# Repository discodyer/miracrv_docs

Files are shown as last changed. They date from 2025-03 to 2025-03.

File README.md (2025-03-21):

# MiracRV_docs

琪迹小车相关文档教程集合

## 硬件组成部分

这部分描述了如何从零开始制作小车底盘

### 生产文件（3D打印/激光切割）

生产文件在manufacture文件夹中，包含：

- 小车底板图纸
- 无刷电机X减速器连接固定片
- 降压模块安装座
- 镭神N10P激光雷达固定座

部分零件需要额外说明，请查看[README](manufacture/README.md)

### 外购零件

外购零件清单（TODO）

### 组装

TODO

## Q&A

>Q1:从设想画图到拿到板子实现测试软件功能，小车的制作整体时间

>小车是从2025年2月7号春节后开始着手制作的，大概是到2月18号硬件部分都组装制作完成

>Q2：哪些部分是自己设计的，以及为什么要自己设计而不是使用已有的配件

>小车的上下层铝板还有无刷电机和减速器的连接板，是我自己设计并找淘宝店铺切割制作的，自己设计的原因是网上的小车底板价格较贵，并且孔位不能满足DIY的需要，我自己设计的小车，兼容了几种常见的激光雷达孔位，同时兼容meles和licheepi 4a还有MATX主板的孔位等。  
设计小车底板的图纸花费的时间并不算多，只花两天就全部设计完成了。
无刷电机和减速器的连接板是小车动力装置的一个重要零件，因为淘宝上没有卖合适的无刷电机+减速器的组合套装，正好看到淘宝上有卖一款给直流电机使用的减速器，但是电机轴兼容3.5mm的，所以我买了相同大小出轴的无刷电机，并且设计了一个连接板将无刷电机和减速器拼接起来，组装了无刷电机减速器。  
这样做的主要原因是成本低廉，并且由于采用了航模无刷电机驱动，转速相对较为稳定。并且可以直接复用无人机的飞控和电调。

>Q3：小车的软硬件详细参数（包括电机、开发板、轮胎、传感器、搭载了什么软件等）

>电机使用了N2830 1300KV电机，使用AM32四合一电调，减速器使用的是27：1的减速器。  
开发板使用的是RISC-V开发板 MilkV meles，运行了RevyOS。
轮胎使用的是麦克纳姆轮，使用的飞控是微空MicoAir743 V2飞控，使用的是自己编译的ArduRover小车固件。

> Q4：列举出小车目前已经实现的功能

>目前可以实现基本运动控制，meles开发板可以在RevyOS上运行ROS2 humble的软件包。雷达没有提供驱动，所以暂时没有使用Cartographer建图，后续会换一个激光雷达继续。

>Q5: 这个DIY过程对你有什么收获和帮助，开发中有哪些因为DIY而产生的困难，以及有哪些因为DIY而带来的特别的好处

>DIY的过程中，因为公司不能使用盗版软件，所以学习了Fusion360，但是这个设计软件在草图比较复杂的时候非常卡顿，并且有一些BUG，不过还是勉强画完了。后续切割完成后，发现了几处可以修改的地方，下一个版本可以吸取经验。激光雷达一开始是在我的电脑上的虚拟机里测试的，但是我后来才发现，厂商提供的SDK是静态编译的库，所以没办法在RISC-V架构上编译。硬件测试过程也遇到过一些问题，最开始使用的电调质量有问题，烧毁了一个电机和我的一块飞控板。

>Q6：小车未来的完善计划

>未来会在小车上充分测试ROS2在RISC-V架构上的功能，并且使用激光雷达在ROS2上实现建图导航等功能

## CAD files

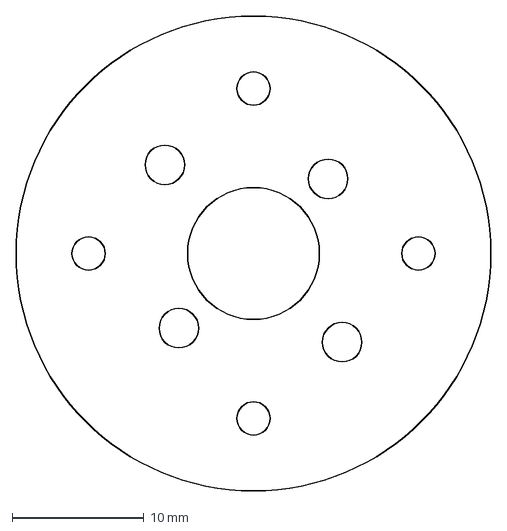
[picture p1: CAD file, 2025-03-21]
manufacture/电机固定片.dxf
36.0 x 36.0 mm

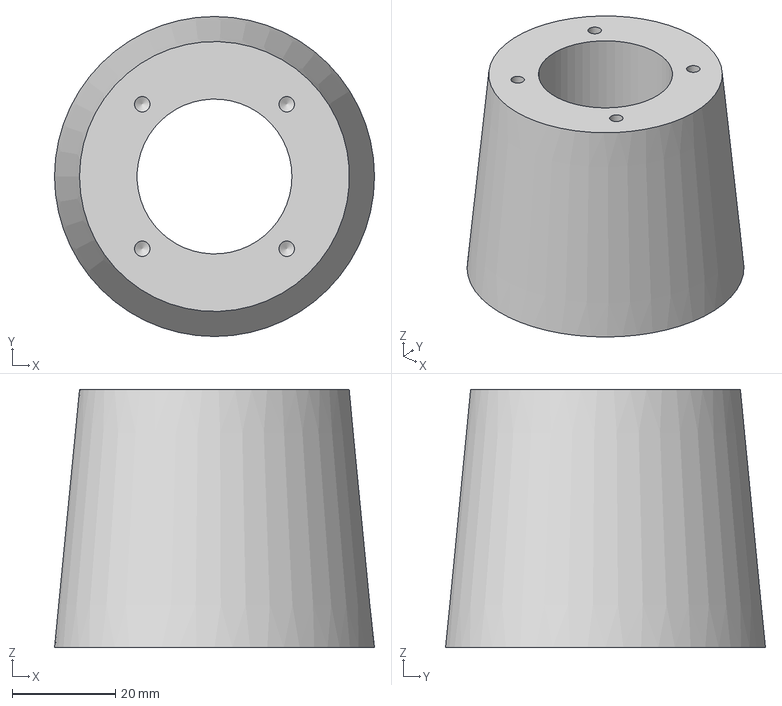
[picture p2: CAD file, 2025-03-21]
manufacture/镭神N10P激光雷达固定座.step
62.0 x 62.0 x 50.0 mm

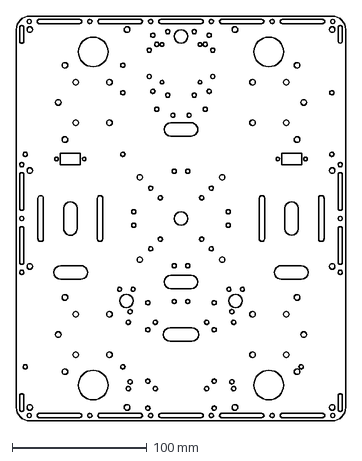
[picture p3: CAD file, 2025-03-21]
manufacture/麦轮小车底盘上板.dxf
244.0 x 300.0 mm

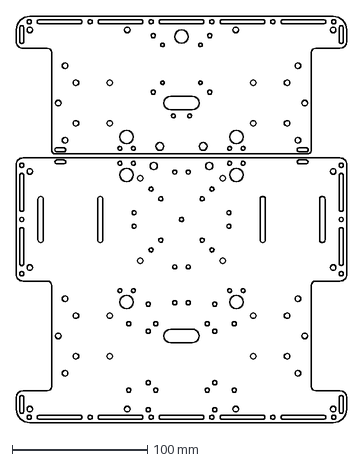
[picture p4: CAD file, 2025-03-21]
manufacture/麦轮小车底盘下板(两个件).dxf
244.0 x 300.0 mm

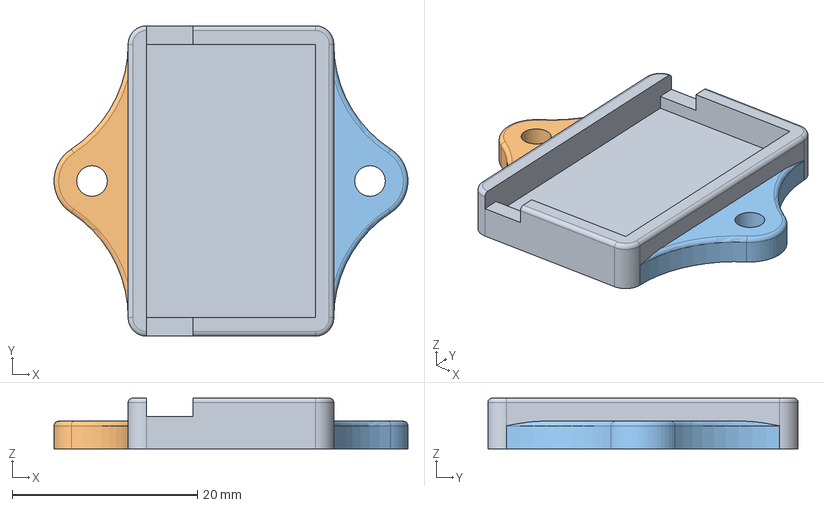
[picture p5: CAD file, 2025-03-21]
manufacture/降压模块安装座.step
38.2 x 33.5 x 5.50 mm

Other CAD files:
manufacture/电机固定片-可编辑.f3d
manufacture/镭神N10P激光雷达固定座-可编辑.f3d
manufacture/镭神N10P激光雷达固定座.stl
manufacture/降压模块安装座-可编辑.f3d
manufacture/降压模块安装座.stl
manufacture/麦轮小车底盘上板-可编辑.f3d
manufacture/麦轮小车底盘下板-可编辑.f3d

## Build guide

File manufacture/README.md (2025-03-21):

# 生产文件说明

## 小车底板图纸

兼容了几种常见的激光雷达孔位，同时兼容`meles`、`licheepi 4a`还有MATX主板的孔位

图纸包含上下两部分，其中下层板有前后两部分组成，可编辑文件可以用Fusion360打开（会很卡）

- [麦轮小车底盘上板-可编辑](麦轮小车底盘上板-可编辑.f3d) 
- [麦轮小车底盘上板-生产文件](麦轮小车底盘上板.dxf) 
- [麦轮小车底盘下板-可编辑](麦轮小车底盘下板-可编辑.f3d) 
- [麦轮小车底盘下板-生产文件(包含两个件)](麦轮小车底盘下板(两个件).dxf)

零件有一些已知的问题：急停开关距离开发板的位置过近，激光雷达孔位太靠前导致安装后会凸出去

## 无刷电机X减速器连接固定片

无刷电机使用的是[N2830 1300kv 后出轴3.17mm轴径](https://item.taobao.com/item.htm?_u=l2nf4lkkc6e8&id=776568563843)，匹配的[36mm行星齿轮减速器](https://detail.tmall.com/item.htm?_u=l2nf4lkk9e62&id=620401236914)减速比选择的是27：1。

使用的是3mm厚不锈钢加工，需要攻丝+倒角

靠近外面的四个孔是对称的，需要攻M3螺纹。靠近内侧的四个孔两两对称，需要倒角但是不用攻丝。

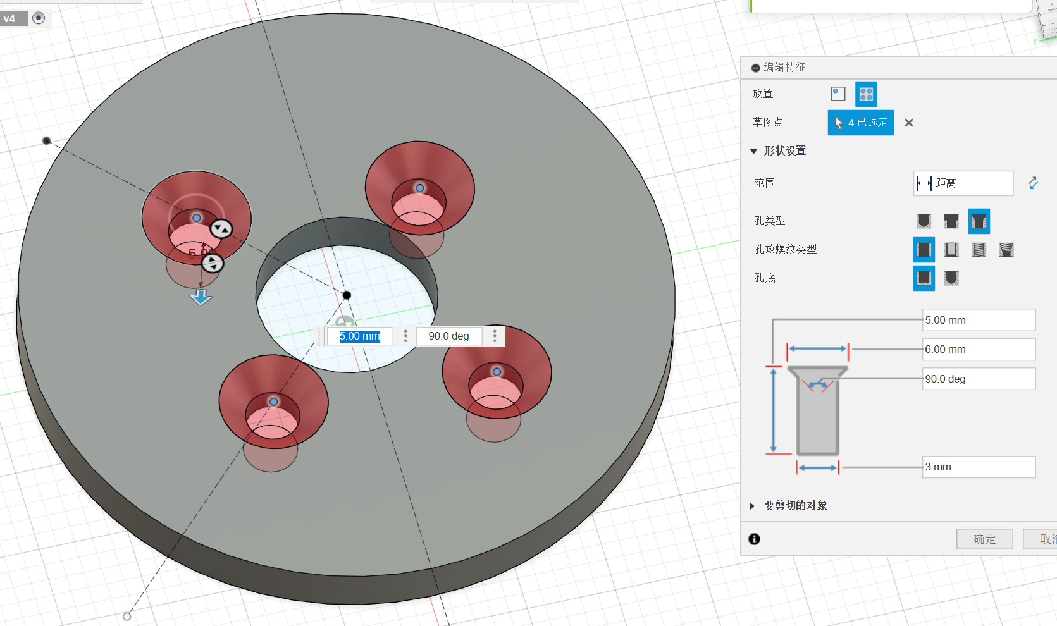
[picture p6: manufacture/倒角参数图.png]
倒角参数图


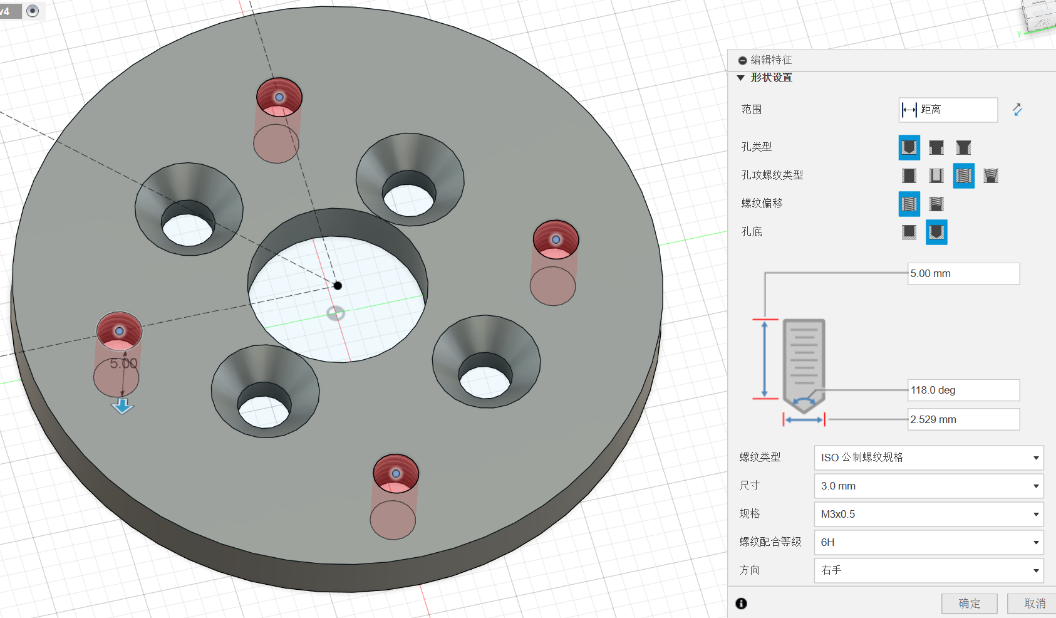
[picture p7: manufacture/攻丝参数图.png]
攻丝参数图


- [电机固定片-可编辑](电机固定片-可编辑.f3d)
- [电机固定片-生产文件](电机固定片.dxf)

## 降压模块安装座

降压模块我使用的是[这款](https://item.taobao.com/item.htm?_u=l2nf4lkk0252&id=831235040211)，也可以使用其他品牌的降压模块。主要需要注意的是输入电压范围最好是50V以上或者标明6S锂电池可用，防止锂电池尖峰电压击穿导致后级短路。

- [降压模块安装座-可编辑](降压模块安装座-可编辑.f3d)
- [降压模块安装座-step](降压模块安装座.step)
- [降压模块安装座-stl](降压模块安装座.stl)

## 镭神N10P激光雷达固定座

这个就是一个增高垫，可以给N10或者N10P使用，需要配合使用M2和M3的热熔螺母，或者直接用胶带也可以

- [镭神N10P激光雷达固定座-可编辑](镭神N10P激光雷达固定座-可编辑.f3d)
- [镭神N10P激光雷达固定座-step](镭神N10P激光雷达固定座.step)
- [镭神N10P激光雷达固定座-stl](镭神N10P激光雷达固定座.stl)
